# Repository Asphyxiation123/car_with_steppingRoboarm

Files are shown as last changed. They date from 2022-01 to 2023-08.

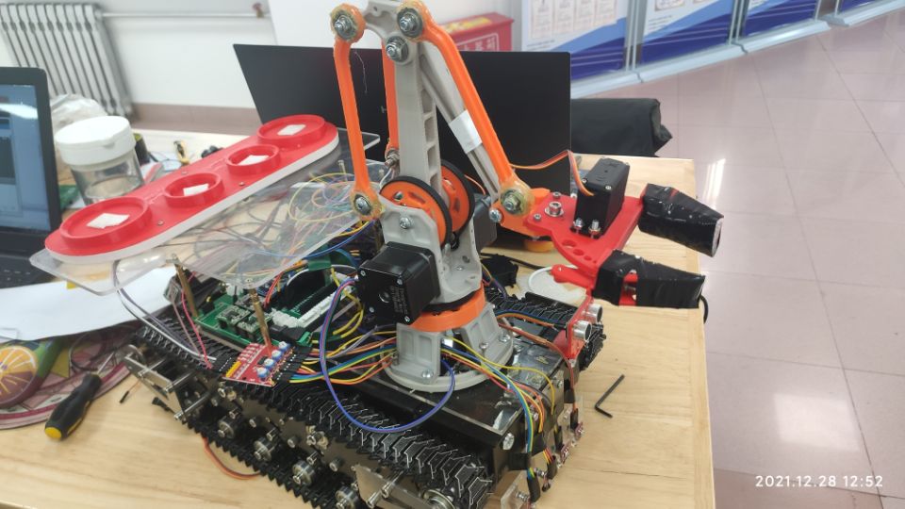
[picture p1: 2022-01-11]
【07】视频图片/图片/小车整体装配图.jpg

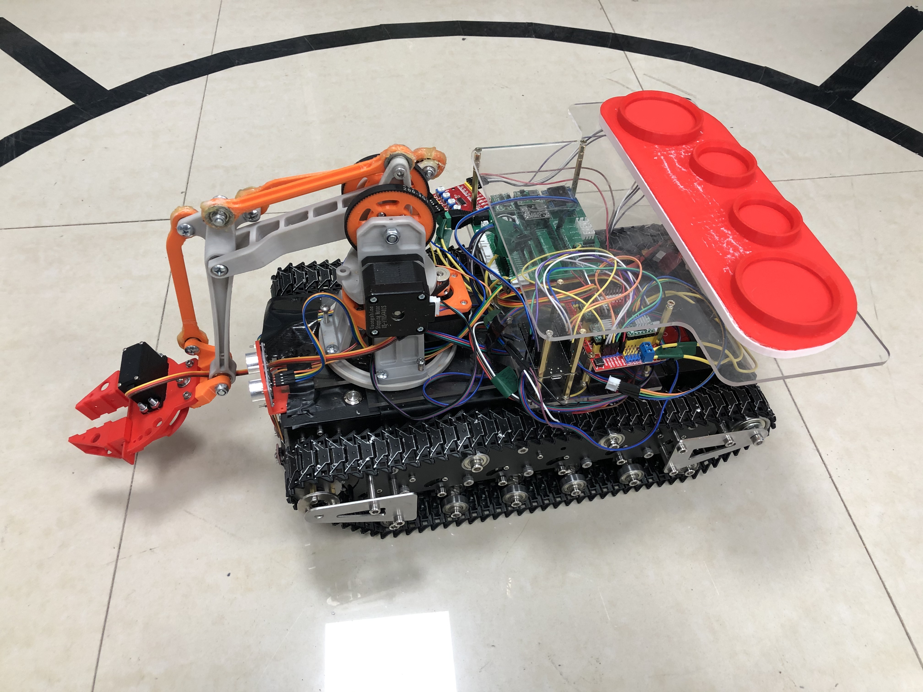
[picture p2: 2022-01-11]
【07】视频图片/图片/小车整体装配图2.jpg

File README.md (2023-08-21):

# car_with_stepperRoboarm
## 1. what's this
This is an course design in 2021,@YanShan University mechatronics engineering,
本仓库存放着自己带机械臂的循迹寻迹小车代码、模型，其借助点灯科技Blink还具有物联网功能。
## 2. 本代码结构
代码主要分为两部分，即Stm32主控制机械结构+esp32上传数据至电灯科技构成物联网系统,分别使用C与C++编写。小车控制用STM32实现，机械臂示教、控制与小车状态显示用ESP32控制。
### 2.1 物联网组态界面框架
其中物联网架构使用的是较为成熟的点灯科技自研的MQTT-UI界面通讯框架，使用方式与QT基本类似，相关资料见点灯科技官网官网。本此项目只要使用物联网组态界面进行小车所在节点实时同步与步进电机机械臂调试。
<video src="【07】视频图片/视频/蓝牙调试机械臂.mp4" controls></video>

### 2.2小车框架
小车运行逻辑为流程运行，但提前根据地图特征将地图分为数个节点，小车在不同节点上运行不同的流程逻辑，具体请见`[01]文档材料`部分。
# 文件架构分析
文件架构以在文件夹标题上有所体现，其中说明文档和介绍ppt可直接见`[01]文档材料`和`[02]PPT汇报`的最终版本，中间版本为进度汇报内容
机械部分图纸见`[03]二维图纸`，PCB电气部分图纸见`[06]嵌入式控制系统`的`电气原理图`部分。
.  
.  
  
.  
.1
.1
.
.
.1

.  
.  
.  
.  
.  

本课程设计的全部代码都由本人完成，真是见鬼，三个队友两个考研一个考公，我没猝死真是太好了。
2022.8.21：抱歉，其实我并不想抱怨上述内容，因为实际情况愿彼此

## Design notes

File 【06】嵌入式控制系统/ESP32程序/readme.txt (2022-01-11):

想要完整地打开项目文件请先按照其他中的教程或按照网络教程 https://www.bilibili.com/video/BV1tv411w74d?from=search&seid=10236622600450991913&spm_id_from=333.337.0.0
搭建好vscode+plateformio的环境，导入项目即可

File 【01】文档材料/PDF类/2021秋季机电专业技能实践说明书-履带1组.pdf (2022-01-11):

# 燕山大学

# 专 业 技 能 实 践 说 明 书

题 | 目： 智能化产线单元设计与制作——带取样
| AGV

### 学院（系）： 机械工程学院

### 年 级 专 业 ： 18 级机械电子工程

组 | 号： 5-履带 1 组
学 号 | 姓 名 | 成 绩
201811010426 | 陈嘉琛（70%）
201811010240 | 王玥灏（10%）
201811010022 | 刘欣源（10%）
201811010241 | 徐世杰（10%）
指 导 教 师 ： | 张连东 李玉昆
日 | 期： | 2021.12

## 燕山大学专业技能实践任务书

院（系）：机械工程学院 | 基层教学单位：机械电子工程系
组号 | 5 | 学生姓名 | 陈嘉琛
题目 | 智能化产线系统集成—履带取样 AGV
实 践 目 标 | 法律及环境等因素进行产品再开发，通过编写完整的程序，进行机器人运动控制规划，对作业过 程进行模拟仿真，最终高效地完成既定的协同作业任务。
实 践 要 求 | （1）运用现代信息技术获取产品相关信息； （2）动作特点能够充分展示机器人或 AGV 系统的结构特点，体现系统化设计思想； （3）整体方案要体现工作效率和经济性； （4）充分体现协同作业和团队合作； （5）动作时间 3-5 分钟。
工 作 量 | （1）资料查阅、方案准备、素材整理； （2）详细分析机器人系统的硬件和软件功能，制定运动控制方案； （3）完成机器人动作的总体规划； （4）编制程序设计流程图； （5）编写程序代码，控制机器人实现规划的动作； （6）程序调试、预演； （7）撰写专业综合训练说明书； （8）完成机器人规划动作的现场展示。
工 作 计 划 | （1）资料查阅、分析总结，所需天数 1 天 （2）运动控制方案设计，所需天数 2 天 （3）机器人动作的总体规划，所需天数 2 天 （4）程序流程图的设计，所需天数 1 天 （5）控制程序编码，所需天数 4 天 （6）程序调试，所需天数 2 天 （7）撰写综合训练说明书，所需天数 2 天 （8）答辩考核、演示，所需天数 1 天
参考 资料 | 通过校园网在我校订阅的电子资料库中可以搜索到大量的有关运动控制、单片机编程的参考 资料。同学们也可到学校的图书馆查找纸质期刊资料。机械学院的计算机中心上班时间免费对本 院学生开放，查阅外网资料。
指导教师签字 | | 基层教学单位主任签字

基于《机电产品设计》二级项目制作的智能机器人机械本体、传感检测、驱动及控制系统， 充分查阅文献，基于工程需求、作业任务、运动轨迹、信息交互等任务，同时考虑社会、安全、

说明：此表一式四份，学生、指导教师、基层教学单位、系部各一份。

年 月 日

## 燕山大学专业综合训练评审意见表

指导教师评语：

成绩：

指导教师：

年 | 月 | 日

答辩小组评语：

成绩：

评阅人：

年 | 月 | 日

课程设计总成绩：

答辩小组成员签字：

年 | 月 | 日

燕山大学专业综合训练说明书

4

目录

5

摘要

AGV 即自动导引小车,它多位一体,集结了当今科技领域先进的理论和应用技术,综 合了声、光、电、计算机等技术。AGV 具有灵活可靠、柔性化好、效率高、操作简便、 可控性强等许多优点,因此在柔性制造系统和自动化工厂中得到了广泛的应用,极大地提 高了企业的生产制造效率和自动化程度。将来的 AGV 必然向着更为简捷高效的方向发 展,会得到进一步推广,其应用领域也必然会随之变的更加广泛。 本项目综合研究分析了国内外 AGV 的发展情况和现状,并根据所学知识自主设计一 辆履带式 AGV 小车。主要设计工作有:机械总体方案设计（履带式底盘和机械臂的设计 或选型）、驱动电机的选取（底盘运行电机及机械臂运动所需电机）、各模块功能设计 选取（传感器、32 系统板、减压模块等）、各模块的实际连接设计、各零部件的强度校 核、基本控制系统分析、软件系统整体方案设计、硬件电路分析与绘制、小车运动学和 动力学分析、控制系统设计以及路径行驶规划策略。最终设计的物流小车能够实现自主 导引运行、运动轨迹的控制、自动循迹及避障、物联网监控组态、按照要求抓取和运输 工件等功能,目标是使其能够模拟现有的工厂实际使用的 AGV 物料运输小车，并绘制各 零件及外部电路原理图、机械装配图及相应的报告，熟悉前沿自动化控制与物联网监控 技术，完成此次项目。
关键词: 履带 AGV 小车 运动分析 自动控制 机械设计 物联网

6

## 第 1 章 产线工作方案介绍

### 1.1 产线简介 1.1.1 硬件系统框图

在整个产线的工作任务中，以 STM32F103C8T6 最小系统板为主控板，接收超声波 模块、四路红外循迹模块、扫码模块的信息，去控制履带底盘、机械臂、末端执行机构 的运行。

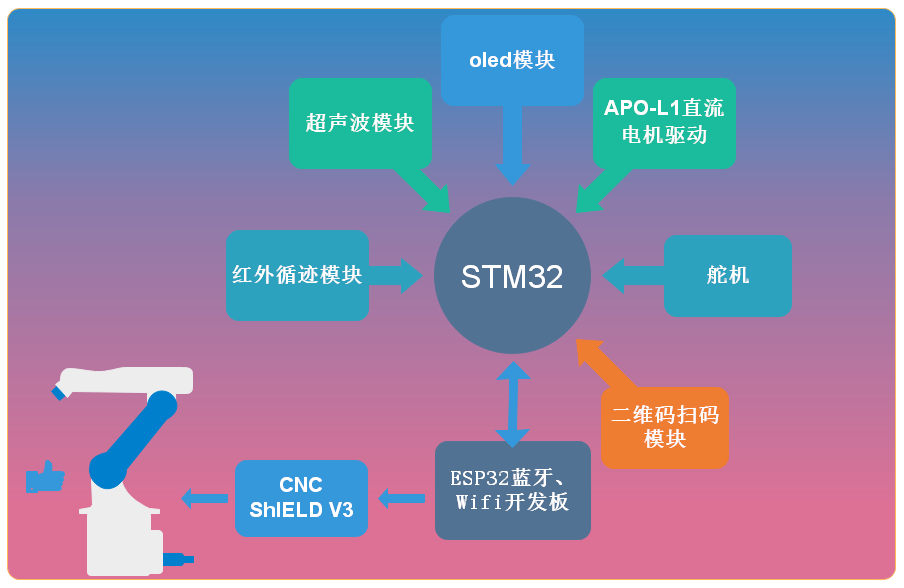
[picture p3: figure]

图 1.1 硬件系统框图

### 1.1.2 各单元硬件功能

表 1 各单元硬件功能

硬件 | 型号 | 功能
单片机 | STM32F103C8T6 | 主控单元，协调各模块的工作
固定降压模块 | MP1584EN（固定 3.3V） | 将电池提供的 12V 降为 3.3V，为板载模块供电
可调降压模块 | MP1584EN（0.8~22V 可调） | 为舵机组接口单独供电，保证舵机的稳定运行
直流电机驱动模块 | APO-L1 | 驱动底盘的两个直流电机
步进电机驱动模块 | A4988 | 驱动机械臂的三个步进电机
末端手爪驱动模块 | MG90S | 驱动末端手爪的张合
红外循迹模块 | 四路红外循迹模块 | 使小车检测并沿地面黑色迹线行驶
超声波模块 | HC-SR04 | 检测前方物体距离，以便停车避障
扫码模块 | SH-50 | 识别二维码，获取所需夹取的物料信息
显示模块 | 0.96inc OLED（IIC 显示屏） | 将关键信息显示，以便查看
Wifi 蓝牙模块 | ESP32 | 远程操控机械臂

7

### 1.2 产线单元的设计与实现

由于前期已经进行过各模块的选型，因此现阶段主要是根据场地任务要求，确定小 车的运行情况。

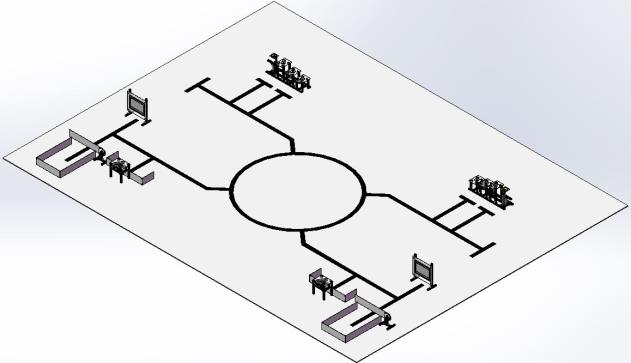
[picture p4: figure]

图 1.2 简化的场地模型

### 1.2.1 陈嘉琛同学方案设计及分析

AGV 履带小车产线单元，以 STM32F103C8T6 最小系统板为主控板，搭配超声波模 块、四路红外循迹模块、扫码模块，等外部传感设备，直流电机及其驱动器控制履带底 盘，步进电机及其驱动器控制机械臂和末端执行机构的运行。 开启开关后，超声波模块检测到开门后，STM32F103C8T6 最小系统板控制小车沿 着红外循迹模块识别到的路线到达扫码区扫描二维码，二维码中包含小车需要夹取货物 的信息。
然后继续寻迹至仓库区，使用自己设计的机械手按照二维码信息抓取预先放置好的 物块，接着小车携带货物沿预定路线返回。寻迹至组装区，小车在平台中心放料，完成 后返回仓库区重复取放货 2 次。

### 1.2.2 王玥灏同学方案设计及分析

AGV 履带小车产线单元，以 STM32F103C8T6 最小系统板为主控板，搭配超 声波模块进行避障功能、摄像头模块进行循迹和扫码功能，直流电机及其驱 动器控制履带底盘，步进电机及其驱动器控制机械臂和末端执行机构的运行。 开启开关后，超声波模块检测到开门后，STM32F103C8T6 最小系统板控制小车 沿着摄像头模块识别到的路线到达扫码区用摄像头扫描二维码，二维码中包 含小车需要夹取货物的信息。然后摄像头继续寻迹至仓库区，使用自己设计 的机械手按照摄像头扫描到的二维码信息抓取预先放置好的物块，接着小车 携带货物沿预定路线返回。寻迹至组装区，小车在平台中心放料，完成后返 回仓库区重复取放货 2 次。

### 1.2.3 刘欣源同学方案设计及分析

AGV 履带小车产线单元，以 STM32F103C8T6 最小系统板为主控板，搭配超声波模 块、四路红外循迹模块、扫码模块，等外部传感设备，直流电机及其驱动器控制履带底 盘，步进电机及其驱动器控制机械臂和末端执行机构的运行。 开启开关后，小车通过红外循迹模块识别并跟踪路线到达扫码区扫描二维码获取所 需夹取的物料，然后继续寻迹至仓库区，使用自己设计的机械手按照二维码信息抓取预

8

先放置好的物块，将所有需要夹取的物块放置小车上的货舱中，接着小车携带货物沿预 定路线返回。寻迹至组装区，小车将货舱中的物料放至平台中心，完成后返回至启动区。

### 1.2.4 徐世杰同学方案设计及分析

AGV 履带小车产线单元，以 STM32F103C8T6 最小系统板为主控板，搭配超声波模 块、四路红外循迹模块、扫码模块，等外部传感设备，直流电机及其驱动器控制履带底 盘，步进电机及其驱动器控制机械臂和末端吸盘的运行。
末端执行机构采用吸盘来进行对物块的抓取和释放，在接触物体时气泵吸气，吸盘 内部产生气压，将物块牢牢吸住，到达目标地点后放气，释放物块。采用气泵的优点有： 排放绿色无污染，物块抓取的程序设计更为简单，操作更方便。

### 1.2.5 小组方案讨论

陈嘉琛同学：王玥灏同学的方案中采用摄像头识别路线的方式虽然对于路线的跟踪更与 加明确和清晰，但较红外循迹而言过于复杂，不便于对设备的设计与调试。 王玥灏同学：刘欣源同学的方案一次抓取两个物块，对于大小物块的识别和抓取有一定 困难，且在小车上装货舱会给小车增加负重，若发生物块倾斜甚至倒下的情况，会严重 影响整体的完成速度。
刘欣源同学：徐世杰同学的方案中将夹爪换成了吸盘，吸盘需要增加检查整块的密封性， 在抓取物块时不能发生偏移，否则会发生不能将物块抓起的情况，若物块不规则，吸盘 将不能将物块抓起。
徐世杰同学：陈佳琛同学的方案需要往返抓取物块 2 次，严重增长了整体完成的时间， 远不如采用货舱的方式简便节省时间。

### 1.2.6 小组最终方案

我们最终决定采用以 STM32F103C8T6 最小系统板为主控板，搭配超声波模块、四 路红外循迹模块、扫码模块，等外部传感设备，直流电机及其驱动器控制履带底盘，步 进电机及其驱动器控制机械臂和末端执行机构的运行。采用末端机械爪并添加货舱只需 一次往返就完成的方案。

9

## 第 2 章 单元动作的总体规划详细方案

由图 1.2 所示，整个场地主要由数个转弯以及中间的圆形环岛迹线组成，由此规划 履带小车的整体动作。

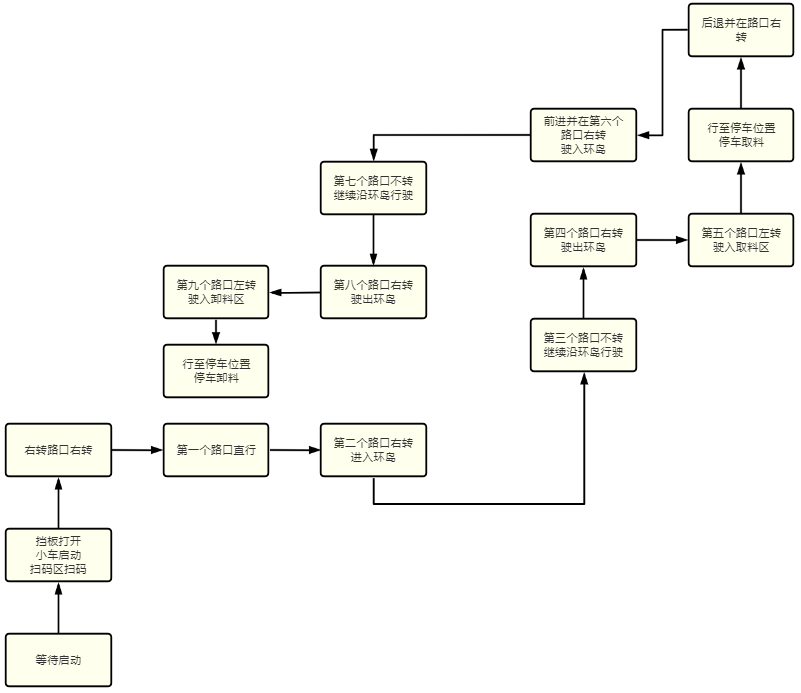
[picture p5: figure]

图 2.1 总体规划框图

## 第 3 章 编制程序设计流程及框图

根据场地组发布的任务要求，AGV 小车的工作流程为：
1、AGV 小车在启动区准备，舵机开门，开始计时，小车出发沿黑线寻迹，前往扫码区 扫描二维码，二维码中包含小车需要夹取货物的信息。
2、寻迹至仓库区，小车到达取货区，使用自带的机械手抓取预先放置好的物块，小车携 带货物返回。
3、寻迹至组装区，小车在平台中心放料，完成后返回仓库区重复取放货 2 次。 4、往返两次后，装箱结束，小车回到出发点，计时结束。
对小车的要求为：
1、小车尺寸，长：不超过 550mm 宽：不超过 360mm：高能正常抓取工件即可。小车 具有机械手用于工件抓取和搬运，手爪抓取最远距离参考需要结合取放货的空间位 置和自身车体大小设计，夹爪抓取物料最小重量为 150g。 2、小车应具有二维码扫描模块和黑线寻迹模块，自行选择红外避障模块和超声波测距模 块等其他传感器。
从 AGV 小车的工作流程及相关的硬件要求中，得出编程的流程：

10

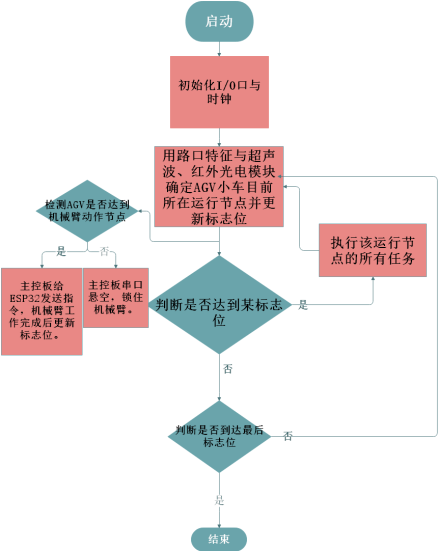
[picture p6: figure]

图 3.1 程序设计流程框图（陈嘉琛）

图 3.2 程序设计流程框图（王玥灏）

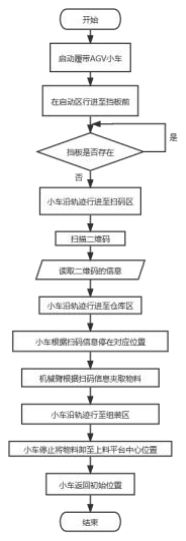
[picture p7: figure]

图 3.3 程序设计流程框图（刘欣源）

11

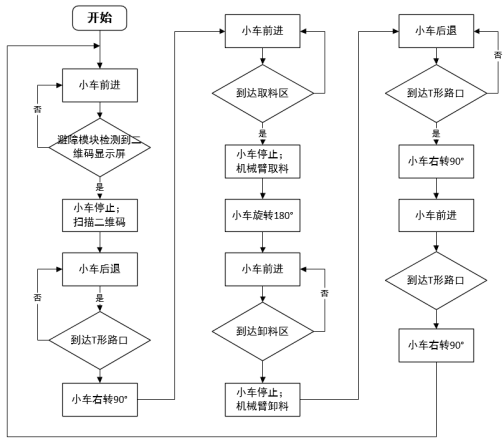
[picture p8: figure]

图 3.4 程序设计流程框图（徐世杰）

## 第4章 编程实现规划动作并编写程序代码

表 2 各硬件模块及负责人

负责人 | 硬件 | 型号
陈嘉琛 | 直流电机驱动模块 | TB6612FNG
| 步进电机驱动模块 | A4988
| Wifi 蓝牙模块 | ESP32
王玥灏 | 超声波模块 | HC-SR04
| 扫码模块 | SH-50
刘欣源 | 显示模块 | 0.96 寸 OLED（IIC 显示屏）
| 红外寻迹模块 | 四路红外循迹模块
徐世杰 | 红外循迹模块 | 四路红外循迹模块
| 末端手爪驱动模块 | MG995

### 4.1 直流电机驱动模块（APO-L1）

直流电机驱动模块用来驱动履带底盘的两个直流减速电机，该模块如图 4.1 所示。

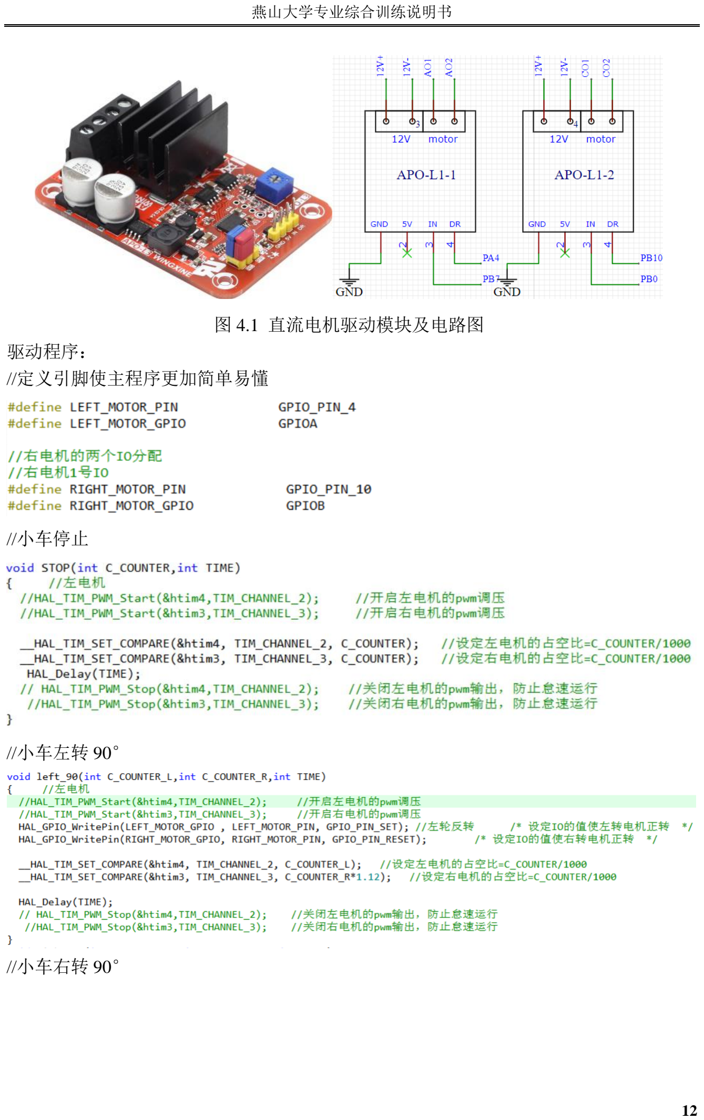
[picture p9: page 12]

12

图 4.1 直流电机驱动模块及电路图
驱动程序：
//定义引脚使主程序更加简单易懂

//小车停止

//小车左转 90°

//小车右转 90°

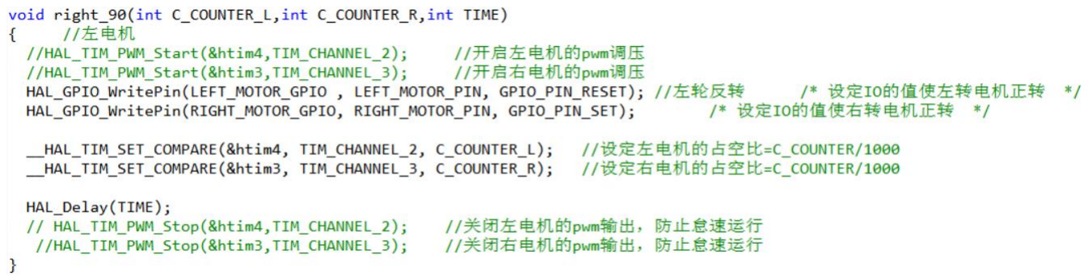
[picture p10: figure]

13

//小车掉头

### 4.2 步进电机驱动模块（A4988）

步进电机驱动模块用来驱动机械臂的三个步进电机，控制机械臂的动作，该模块如 图 4.5 所示。

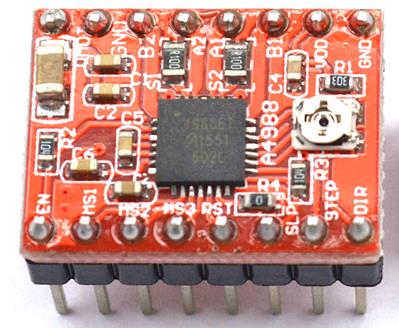
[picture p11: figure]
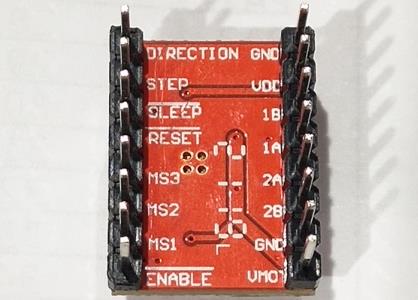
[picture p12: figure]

图 4.2 步进电机驱动模块（A4988）
对于 A4988 来说，ENA 为使能端，低电平有效；STEP 为步进电机信号的输入端， 可以采用 PWM 波输入，也可以采用 IO 引脚高低电平转换；MS1、MS2、MS3 控制一 个脉冲旋转多少度，分别是全步进，1/2 步进，1/4 步进，1/8 步进，1/16 步进模式，如 表所示；DIR 为步进电机方向控制 IO 高电平为顺时针，低电平为逆时针；VDD 为模块 的逻辑电压 3V3 或 5V，VDD 必须接电；VMOT 为步进电机的输入电压（8V-35V）；1A、 1B 为同一相，2A、2B 为同一相，不能接反，否则电机会出现抖动的情况。对于步进电 机同一相的确定方法是：将电压表打到蜂鸣器档位，将正负表笔随意接步进电机的两个 引脚，若蜂鸣器响起，则该两引脚为一相。
综上，控制 MS1、MS2、MS3、STEP、DIR 就可以控制一个步进电机的运行了，甚 至只用 STEP 就可以了。
引脚 | MS1 | MS2 | MS3 | 步进模式
引脚 电平 | L | L | L | 全步进
| H | L | L | 1/2 步进

14

L | H | L | 1/4 步进
H | H | L | 1/8 步进
H | H | H | 1/16 步进
//将接收二维码传递的数据进行转换，确定夹取物块的顺序

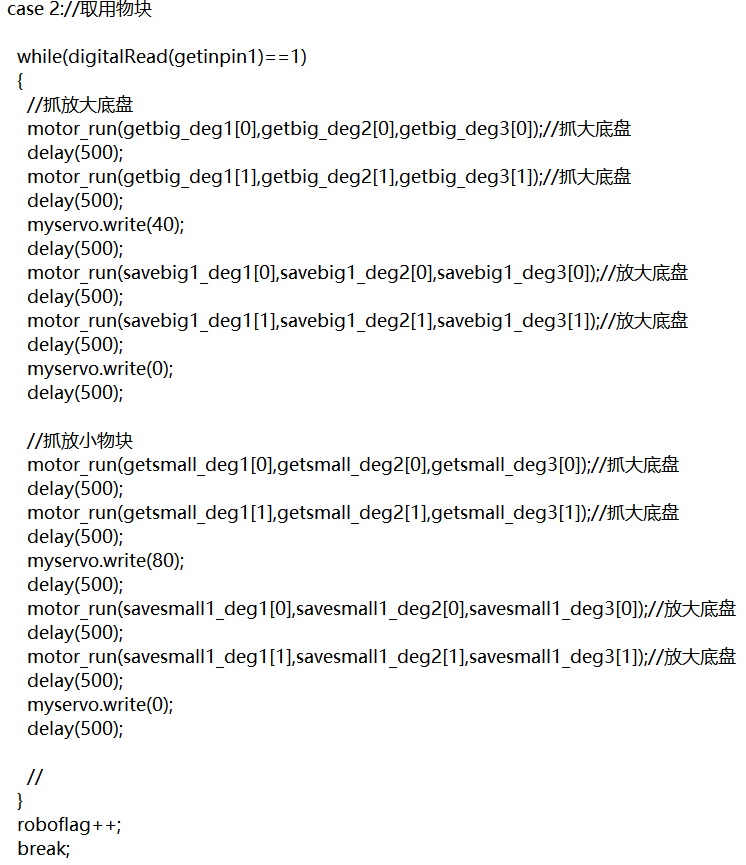
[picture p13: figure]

15

16

17

### 4.3 末端手爪驱动模块（MG995）

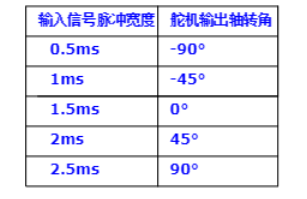
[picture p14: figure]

图 4.3 舵机转角数据图

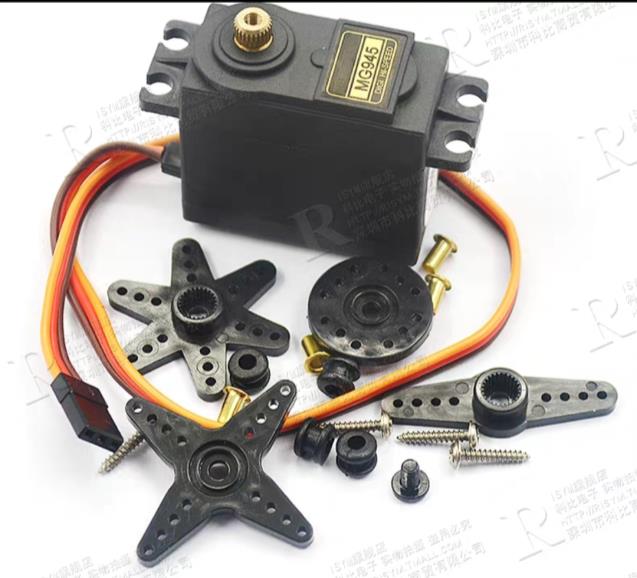
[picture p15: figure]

图 4.4 末端手抓驱动模块
程序已加入步进电机的夹取部分，详细如 4.2 步进电机驱动模块（A4988）所述程序

### 4.4 超声波模块（HC-SP04）

超声波模块装在履带底盘小车的前方，用来检测与前方物体的距离，以便小车及时 减速避让或停车。该模块如图 4.6 所示。

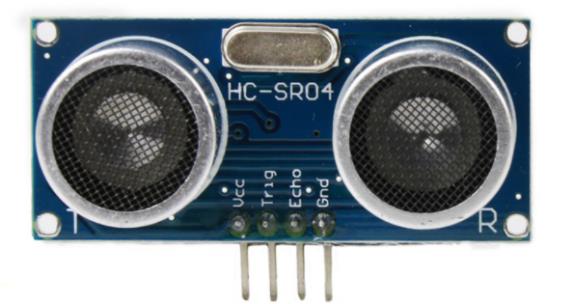
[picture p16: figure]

图 4.5 超声波模块（HC-SR04）
超声波模块程序的编写参考图 4.7 的时序图，时序图表明，只需要提供一个 10uS 以

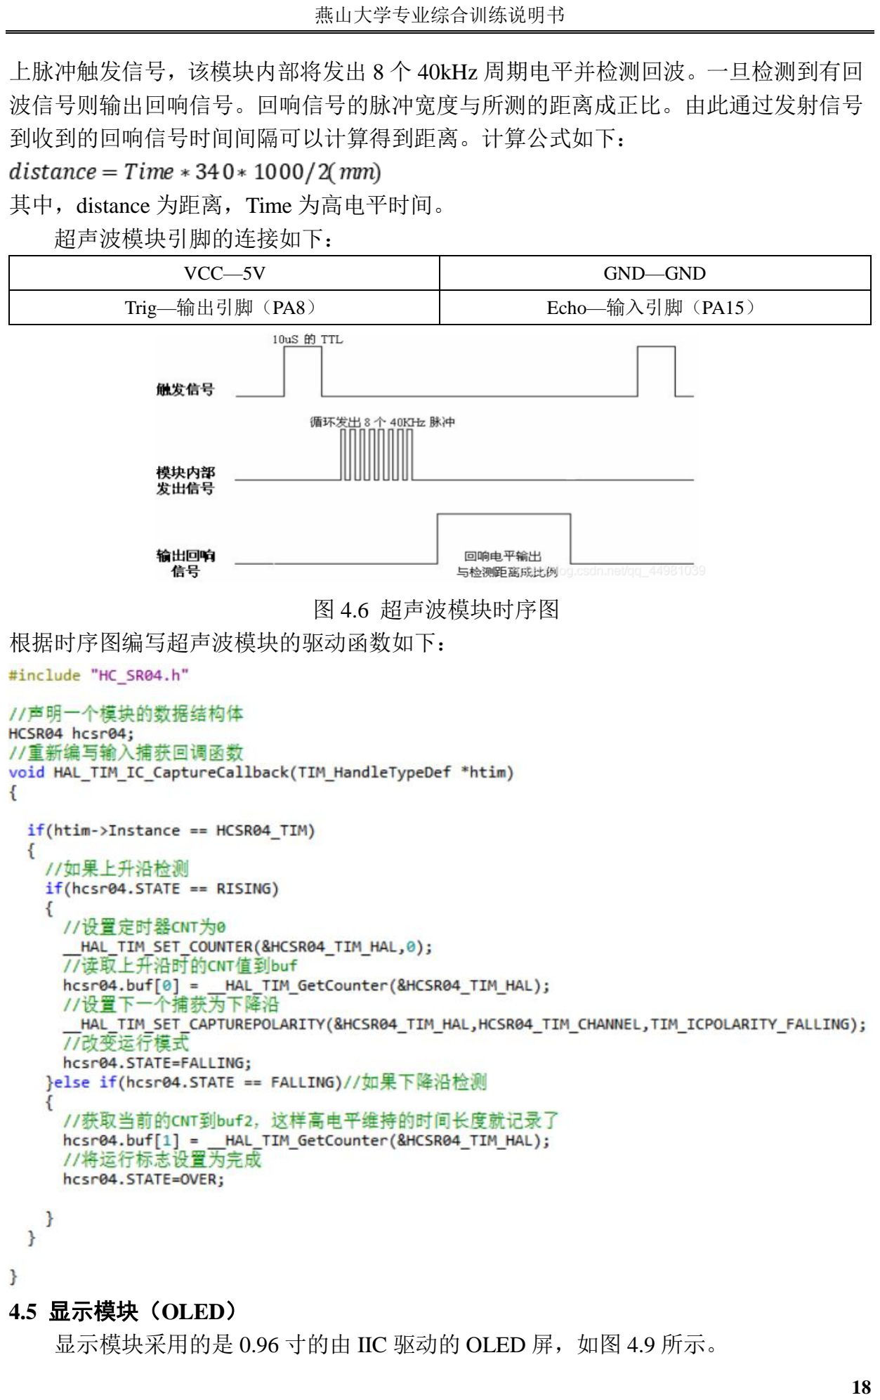
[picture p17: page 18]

18

上脉冲触发信号，该模块内部将发出 8 个 40kHz 周期电平并检测回波。一旦检测到有回 波信号则输出回响信号。回响信号的脉冲宽度与所测的距离成正比。由此通过发射信号 到收到的回响信号时间间隔可以计算得到距离。计算公式如下：

其中，distance 为距离，Time 为高电平时间。
超声波模块引脚的连接如下：
VCC—5V | GND—GND
Trig—输出引脚（PA8） | Echo—输入引脚（PA15）

图 4.6 超声波模块时序图
根据时序图编写超声波模块的驱动函数如下：

### 4.5 显示模块（OLED）

显示模块采用的是 0.96 寸的由 IIC 驱动的 OLED 屏，如图 4.9 所示。

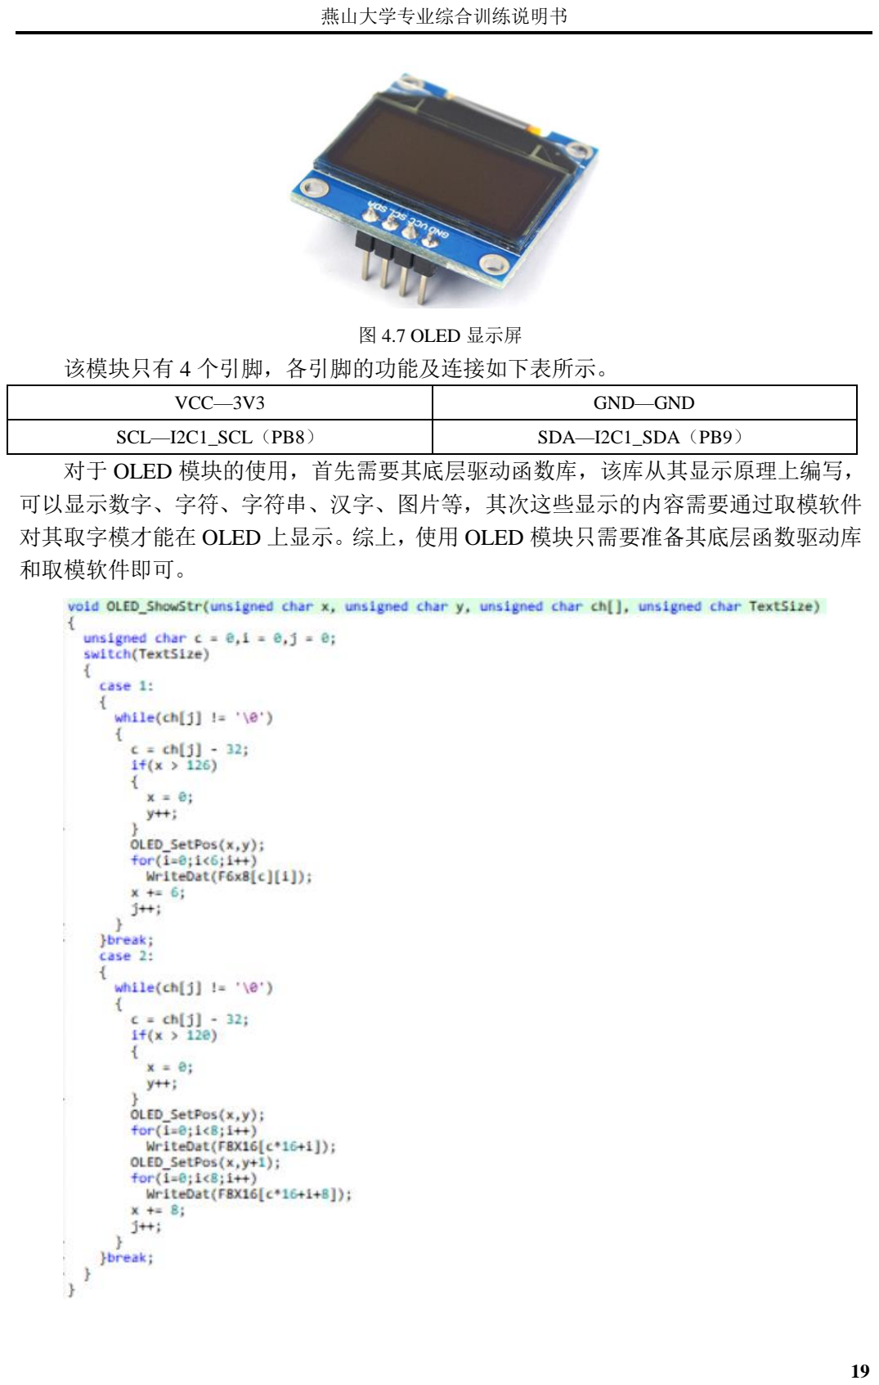
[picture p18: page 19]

19

图 4.7 OLED 显示屏
该模块只有 4 个引脚，各引脚的功能及连接如下表所示。
VCC—3V3 | GND—GND
SCL—I2C1_SCL（PB8） | SDA—I2C1_SDA（PB9）
对于 OLED 模块的使用，首先需要其底层驱动函数库，该库从其显示原理上编写， 可以显示数字、字符、字符串、汉字、图片等，其次这些显示的内容需要通过取模软件 对其取字模才能在 OLED 上显示。综上，使用 OLED 模块只需要准备其底层函数驱动库 和取模软件即可。

20

### 4.6 扫码模块（SH-50）

在场地组的要求中，小车首先要在启动区进行扫码，得到需要夹取的物料的信息， 然后小车才能出发。
扫码模块使用的是上海斯恳赫公司生产的 SH-50 型扫码模块，如图 4.11 所示。该模 块可以直接通过串口将扫码信息发送到上位机，中间无需人为转换。但在项目实施中， 小车要自我识别扫码信息，不能人为操控，因此该模块的使用主要是将扫码得到的信息 进行处理，使单片机能识别。

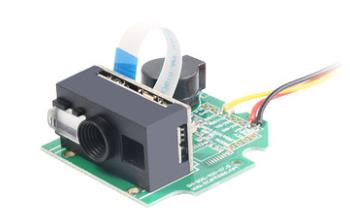
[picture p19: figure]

图 4.8 扫码模块（SH-50）
在该扫码模块上自带串口功能，因此单片机需要通过串口与该模块通讯。如图 4.12 所示，首先在单片机中预设好扫码要得到的信息，以“01234567”为例，将信息进行拆 分提取。

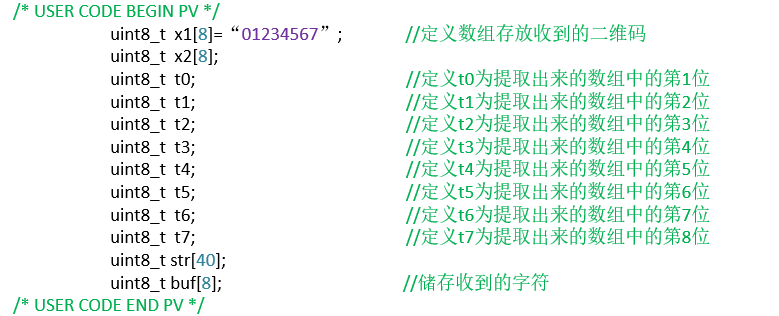
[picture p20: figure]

### 4.7 红外寻迹模块（四路红外循迹模块）

红外循迹模块负责检测地面的黑色迹线，控制履带底盘的前进、左转、右转等动作， 如图 4.14 所示。

21

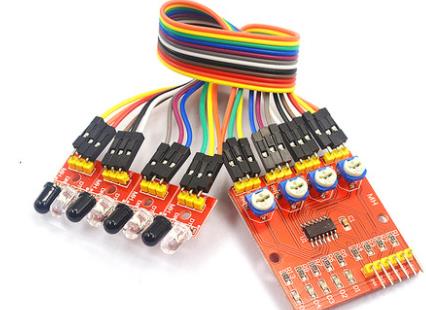
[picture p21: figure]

图 4.9 红外循迹模块（四路红外循迹）
对于该循迹模块，黑色 led 发出红外光，经反射后由白色 led 接收。当物体的颜色较 白时，反射的红外光较多，此时模块上对应的 D 口 led 亮，此时输出低电平；当物体的 颜色较深时，吸收的红外光较多，反射的较少，此时模块上对应的 D 口 led 灭，此时输 出高电平。模块上有对应的电位器，调节电位器即可调节相应循迹模块的灵敏度。因此， 对于该模块的编程，主要是读取相应引脚的高低电平去改变履带底盘电机的转速和转向 即可。
四路红外循迹模块控制履带底盘直流电机的部分程序如图 4.15 所示，当中间两路检 测到高电平时，说明此时为直线，车体居中，底盘直走；当中间两路任意一路为低电平 时，说明此时车体向该路偏转，需要将该路侧的电机转速加大，使其归正，以此类推。

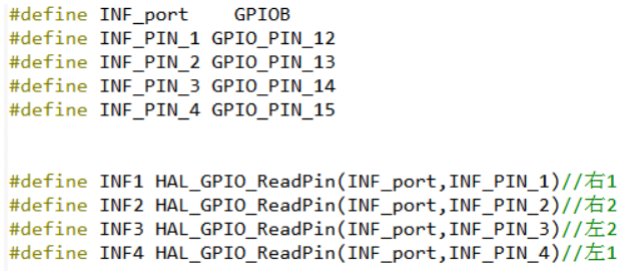
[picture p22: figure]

//小车循迹

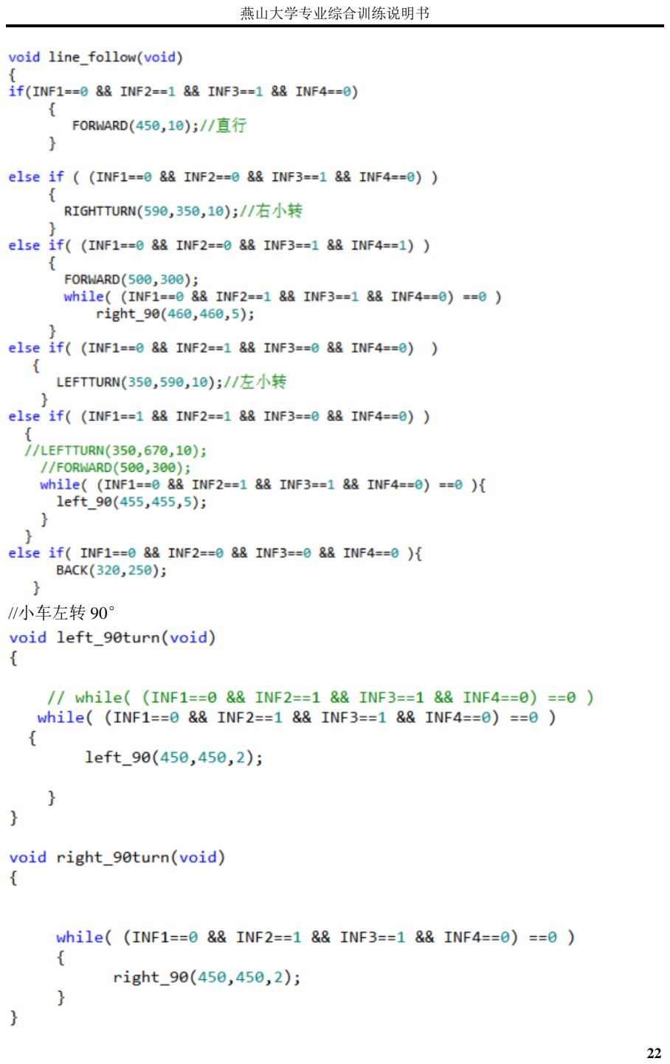
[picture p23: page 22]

22

//小车左转 90°

23

//小车环岛循迹

### 4.8 Wifi 蓝牙模块（ESP32）

Wifi 蓝牙模块 ESP32 用以辅助控制机械臂的运动。

图 4. 10 ESP32 引脚分配功能图

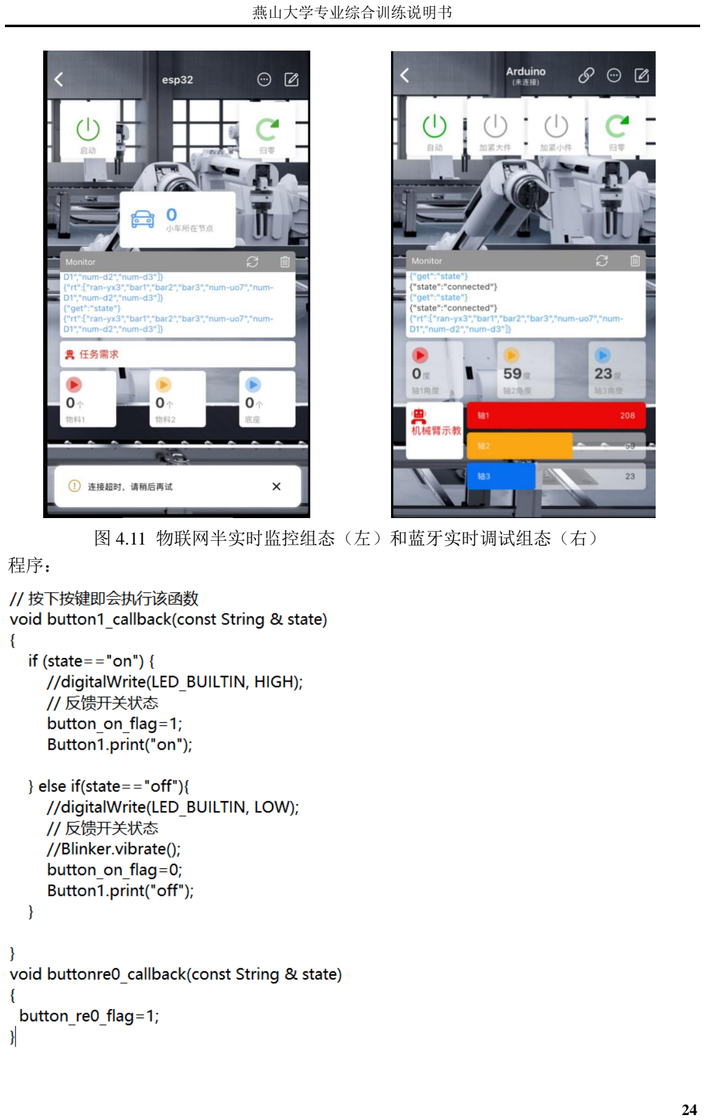
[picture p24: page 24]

24

图 4.11 物联网半实时监控组态（左）和蓝牙实时调试组态（右） 程序：

25

## 第 5 章 程序调试结果及改进

程序调试过程中，对于有些模块，只要给定固定的程序就能够正确运行。因此只对 其中直流电机模块、超声波模块、红外寻迹模块和显示的调试进行阐述。

### 5.1 直流电机模块的调试（陈嘉琛）

在直流电机模块的调试过程中，最开始采用的是 TB6612FNG，多次调试却总是只 有一个履带可以运行，所以想到是否是这种模块的电压太小，所以就更换成了 APO-L1， 发现的确是 TB6612FNG 带不动直流电机。把左右两个直流电机的占空比设置为相同值， 理论上两个直流电机的转速应该相同，但经过数十次的循迹过后，发现在相同占空比的 条件下，履带小车在走直线时，车体总会往左偏，即左轮速度会比右轮速度快。随后经 过数次尝试，找出了合适的占空比，如图 5.1 所示，使履带小车在进行直线循迹时，能 尽量保持在中位。

### 5.2 超声波模块的调试（王玥灏）

在超声波模块的调试中，很重要的一个因素是电源的供给必须是 5V，如果使用的是 3V3 的电源，即使程序编写正确，超声波测出的距离也会不准确或者没有变化，对于排 查程序的错误也会增加很多困难。
最开始是在 NUCLEO 开发板上进行程序的编写实验的，成功驱动之后需要移植到 STM32F103C8T6 最小系统板上，但在移植之后，发现超声波模块不能正常使用，连值 都不能输出。在经过两部分程序及 CubeMX 设置的对比之后发现，NUCLEO 开发板上 自带旁路时钟源，而 STM32F103C8T6 最小系统板上没有，因此照搬 NUCLEO 的设置的 行不通，最后把 HSE 选项选到 Disable 之后，如图 5.3 所示，超声波模块就能正常运行 了。

### 5.3 红外寻迹模块的调试（刘欣源）

红外循迹模块的调试主要是灵敏度和模块之间的间距。红外循迹模块的灵敏度是单 片机能正常触发相关程序的关键，其灵敏度是通过模块上相关 led 小灯的亮灭来体现的， 有一个最大的误区就是当小灯微微亮时，输出的是高电平，很容易导致信号错误，使小 车发生错误判断。所以在调试时，相关 led 小灯只能出现非亮即灭两种情况，否则容易 导致单片机错误判断。另外是在直射光较强时，地面的黑色迹线反射的光线也较强，会 使红外循迹模块接收到相关的红外信号，即把此处判断为低电平，会使小车莫名停车， 但遮挡相关干扰光线之后，就能使小车正常工作。环境过暗也同理，会使红外循迹模块 把本该识别为低电平的地方识别成高电平，使小车误判，因此环境的光线也极为重要。 红外循迹模块的间距的主要是配合场地的 50mm 黑色迹线，在直线情况时，本组使 用中间两个模块位于黑色迹线中间，两边的红外模块在黑色迹线之外，四个红外循迹模 块在水平和竖直方向的同一平面上。若红外循迹模块之间的间距过宽，会使履带小车在 过圆形环岛迹线时，不容易判断路口，进行计数识别；若红外循迹模块之间的间距过窄， 会使履带小车频繁的调整车体姿态，影响履带小车的行走，并且会增大红外循迹模块之 间的干扰，造成误检测。

### 5.4 显示模块的调试（徐世杰）

显示模块即 OLED 模块程序的调试主要是换行显示及动态刷新的程序调试。

26

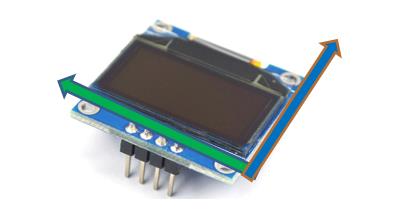
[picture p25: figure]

图 5.1 OLED 模块
换行显示的目的是使 OLED 屏能显示更多相关信息。如图 5.4 所示，在绿色箭头方 向，OLED 有 128 个像素点；在蓝色箭头方向，OLED 分为 8 页，每页共 8 个像素点。 在取模软件输出的字的大小一般为 16×16 个像素的大小，因此可以知道，每个字或数字 等，在绿色箭头方向占 16 个像素点，在蓝色箭头方向占 2 页，所以可以写出换行程序如 图 5.5 所示。

图 5.5 OLED 换行程序（部分）
其次是 OLED 显示动态刷新内容，此功能可以配合超声波模块的测距和检测四路红 外循迹模块的使用。调试的思路是：首先定义一个数组，将外部输入进来的信号存到此 数组之中，再采用 sprintf 函数将其打印，最后通过 OLED 显示函数将其发送到显示页面 上。

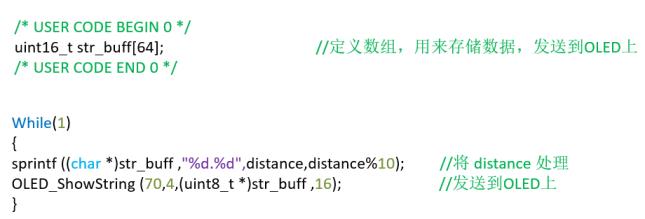
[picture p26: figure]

图 5.2 OLED 动态刷新显示内容

27

## 第 6 章 项目思政心得体会

陈嘉琛：
经过本次二级项目，我们将二级项目中遇到的问题和困难进行了思考总结，对所使用的 stm32cube，keil 等软件和机械臂机器人，还有红外循迹模块，超声波模块等传感器有 了进一步的认识；通过本次二级项目，我们除了提高了软件的操作能力，也明白了团队 合作的重要性，没有大家的共同努力，是无法将本次项目做好的。相信我们日后对待更 加复杂的问题时，也能处理地更加完善。
王玥灏：
通过此次二级项目的实施，我们对机器人技术，机械动力学分析，嵌入式，传感器，机 电一体化等课程有了更深的认识。“纸上得来终觉浅，绝知此事要躬行”。在没有开始 实验之前，对于二级项目有点自己上了就能行的感觉。等到真正的上手操作时，却发现 自己终究是眼高手低，各种各样的问题层出不穷，最终在通力合作下才完成了项目。学 习的路上任重道远，我们要保持终身学习的好习惯，才能站在时代的风口而屹立不倒。 刘欣源：
通过查阅相关文献资料与小组内部讨论，在小组的共同努力下，完成了本次二级项目。 本次项目涉及了嵌入式，机器人技术等课程，对这些学过的课程有了更深刻的认识。二 级项目训练了我们如何查资料及绘图、数据处理、创新能力，培养了我们独立设计机电 一体化产品的能力，提高我们综合应用已有知识解决问题的能和综合素质。同时加强团 队协作能力，促进交流与合作，拓展视野，勇于创新，提高思考与决策水平，形成解决 实际问题的能力和终身学习的能力。
徐世杰：
在本次二级项目中，合理分工，通力合作，每位成员都发挥了自己相对应的价值，对本 次课程设计做出了很大的贡献，我们了收获很多，在设计过程中大家一起讨论，分工合 作，相互帮助，使得项目顺利完成。在这个项目过程中同样也会有很多的意见，通过团 结合作，我们最终完善了这个项目。同时，这次项目使我们把过去一个段时间所学的理 论知识融会贯通，真正了解理论知识在工程实际中的应用，提高了解决实际问题的能力， 锻炼了主动学习及查阅资料的能力。

28

## 参考文献

[1] 闻邦椿 机械设计手册.[M](第一版)，北京，机械工业出版社，2010 年 1 月，
[2] 钱晓捷 [程 楠] 嵌入式系统导论[M]（第四版），北京，电子工业出版社，2020 年 2 月
[3] 许立忠 [周玉林] 机械设计[M] （第三版），北京，中国标准出版社，2019 年 9 月
[4] 龚溎义 [严国良] 设计课程设计图册（第三版），北京，高等教育出版社，2019 年 12 月

29

## 附录 1 程序源代码

//linetracking.h 宏定义部分程序，可以使主程序更简洁 #define INF1 HAL_GPIO_ReadPin(INF_port,INF_PIN_1)//右 1 #define INF2 HAL_GPIO_ReadPin(INF_port,INF_PIN_2)//右 2 #define INF3 HAL_GPIO_ReadPin(INF_port,INF_PIN_3)//左 2 #define INF4 HAL_GPIO_ReadPin(INF_port,INF_PIN_4)//左 1

//linetracking.c 程序

#include "linetracking.h"

#include "motor.h"

#include "stm32f1xx_hal.h"

extern uint8_t flag_reach;
void linetrack(void)
{
if(INF1==0 && INF2==1 && INF3==1 && INF4==0) {
FORWARD(450,10);//直行

}
else if ( (INF1==0 && INF2==0 && INF3==1 && INF4==0) )
{
RIGHTTURN(500,350,10);//右小转

}
else if ( (INF1==0 && INF2==0 && INF3==0 && INF4==1) ||(INF1==0 && INF2==0 && INF3==1 && INF4==1)) {
RIGHTTURN(650,370,10);//右 da 转

}
else if( (INF1==0 && INF2==1 && INF3==0 && INF4==0) ) {
LEFTTURN(350,500,10);//左小转

}
else if( (INF1==1 && INF2==0 && INF3==0 && INF4==0) ||(INF1==1 && INF2==1 && INF3==0 && INF4==0) ) {
LEFTTURN(350,680,10);//左 da 转

}

30

else if(INF1==0 && INF2==0 && INF3==0 && INF4==0) {
STOP(0,100);
BACK(350,400);
}
else if(INF1==1 && INF2==1 && INF3==1 && INF4==1) {
STOP(0,50);//停转

if(INF1==1 && INF2==1 && INF3==1 && INF4==1){ STOP(0,50);//停转

flag_reach=1;
HAL_GPIO_WritePin(led_GPIO_Port,led_Pin,GPIO_PIN_SET); rotate_180(420,420,3000);
while( (INF1==0 && INF2==1 && INF3==1 && INF4==0) ==0 ) rotate_180(420,420,10);
}
}
else if(INF1==1 && INF2==1 && INF3==1 && INF4==0) {
STOP(0,50);//停转

if(INF1==1 && INF2==1 && INF3==1 && INF4==0)
{
while( (INF1==0 && INF2==1 && INF3==1 && INF4==0) ==0 ) left_90(330,580,10);
}
}
void line_follow(void)
{
if(INF1==0 && INF2==1 && INF3==1 && INF4==0) {
FORWARD(450,10);//直行

}

else if ( (INF1==0 && INF2==0 && INF3==1 && INF4==0) ) {
RIGHTTURN(590,350,10);//右小转

}
else if( (INF1==0 && INF2==0 && INF3==1 && INF4==1) ) {

31

FORWARD(500,300);
while( (INF1==0 && INF2==1 && INF3==1 && INF4==0) ==0 ) right_90(460,460,5);
}
else if( (INF1==0 && INF2==1 && INF3==0 && INF4==0) ) {
LEFTTURN(350,590,10);//左小转

}
else if( (INF1==1 && INF2==1 && INF3==0 && INF4==0) ) {
//LEFTTURN(350,670,10);
//FORWARD(500,300);
while( (INF1==0 && INF2==1 && INF3==1 && INF4==0) ==0 ){ left_90(455,455,5);
}
}
else if( INF1==0 && INF2==0 && INF3==0 && INF4==0 ){ BACK(320,250);
}
}
void left_90turn(void)
{
// while( (INF1==0 && INF2==1 && INF3==1 && INF4==0) ==0 ) while( (INF1==0 && INF2==1 && INF3==1 && INF4==0) ==0 )
{
left_90(450,450,2);
}
}
void right_90turn(void)
{
while( (INF1==0 && INF2==1 && INF3==1 && INF4==0) ==0 ) {
right_90(450,450,2);
}
}
void circle_turn(void)
{
if(INF1==0 && INF2==1 && INF3==1 && INF4==0) {

32

FORWARD(420,2);//直行

}
else if ( (INF1==0 && INF2==0 && INF3==1 && INF4==0) ||(INF1==0 && INF2==0 && INF3==1 && INF4==1) ) {
RIGHTTURN(675,350,5);//右小转

}
else if( (INF1==0 && INF2==1 && INF3==0 && INF4==0) ||(INF1==1 && INF2==1 && INF3==0 && INF4==0) ) {
LEFTTURN(350,670,5);//左小转

}
else if( INF1==0 && INF2==0 && INF3==0 && INF4==0 ){ BACK(330,40);
}
}
uint8_t T_check(void)
{
if(INF1==1 && INF2==1 && INF3==1 && INF4==1)
{
STOP(0,50);//停转

if(INF1==1 && INF2==1 && INF3==1 && INF4==1) {
return 1;
}
else
return 0;
}
else
return 0;
}
uint8_t left90_check(void)
{
if(INF1==1 && INF2==1 && INF3==1 && INF4==0)
{
STOP(0,50);//停转

if(INF1==1 && INF2==1 && INF3==1 && INF4==0) {
return 1;

33

}
else
return 0;
}
else
return 0;
}
uint8_t right90_check(void)
{
if(INF1==0 && INF2==1 && INF3==1 && INF4==1)
{
STOP(0,50);//停转

if(INF1==0 && INF2==1 && INF3==1 && INF4==1) {
return 1;
}
else
return 0;
}
else
return 0;
}
uint8_t right_180turn(void)
{
right_90(440,440,800);
while( (INF1==0 && INF2==1 && INF3==1 && INF4==0)==0 ) {
right_90(440,440,2);
}
return 1;
}
void line_follow_slowdown(void)
{
if(INF1==0 && INF2==1 && INF3==1 && INF4==0) {
FORWARD(380,5);//直行

}
else if ( (INF1==0 && INF2==0 && INF3==1 && INF4==0) ) {

34

RIGHTTURN(490,340,10);//右小转

}
else if( (INF1==0 && INF2==0 && INF3==1 && INF4==1) ) {
FORWARD(500,300);
while( (INF1==0 && INF2==1 && INF3==1 && INF4==0) ==0 ) right_90(460,460,5);
}
else if( (INF1==0 && INF2==1 && INF3==0 && INF4==0) ) {
LEFTTURN(340,490,10);//左小转

}
else if( (INF1==1 && INF2==1 && INF3==0 && INF4==0) ) {
//LEFTTURN(350,670,10);
//FORWARD(500,300);
while( (INF1==0 && INF2==1 && INF3==1 && INF4==0) ==0 ){ left_90(455,455,5);
}
}
else if( INF1==0 && INF2==0 && INF3==0 && INF4==0 ){ BACK(320,250);
}
}
uint8_t middle_check(void)
{
if(INF1==0 && INF2==1 && INF3==1 && INF4==0) {

HAL_Delay(20);//
if(INF1==0 && INF2==1 && INF3==1 && INF4==0) {
return 1;
}
else
return 0;
}
else
return 0;

35

}
void dongyidong(void)
{
FORWARD(400,2000);
BACK(400,2000);
left_90(450,450,1000);
right_90(450,450,1000);
}

//motor.c 直流电机运行程序

#include "motor.h"

#include "tim.h"

//左转函数
/* 注：电机输入 IO 口 1 表示正转，0 表示反转
PWM 口输入 0--1000 值进行速度调节

*/
void LEFTTURN(int C_COUNTER_L,int C_COUNTER_R,int TIME_L) { //左电机

//HAL_TIM_PWM_Start(&htim4,TIM_CHANNEL_2);
//开启左电机的 pwm 调压
__HAL_TIM_SET_COMPARE(&htim4, | TIM_CHANNEL_2, | C_COUNTER_L);
//设定左电机的占空比=C_COUNTER/1000
HAL_GPIO_WritePin(LEFT_MOTOR_GPIO | , | LEFT_MOTOR_PIN,
GPIO_PIN_RESET); //左轮正转 | /* 设定 IO 的值使左转电机正转或反转 */
//右电机

// HAL_TIM_PWM_Start(&htim3,TIM_CHANNEL_3);
//开启右电机的 pwm 调压

__HAL_TIM_SET_COMPARE(&htim3, TIM_CHANNEL_3, C_COUNTER_R*1.2); //设定右电机的占空比=C_COUNTER/1000

HAL_GPIO_WritePin(RIGHT_MOTOR_GPIO, | RIGHT_MOTOR_PIN,
GPIO_PIN_RESET); | /* 设定 IO 的值使右转电机正转或反转 */
//设定运行时间

HAL_Delay(TIME_L);
// | HAL_TIM_PWM_Stop(&htim4,TIM_CHANNEL_2); | //关闭左电机的 pwm 输
出，防止怠速运行
// | HAL_TIM_PWM_Stop(&htim3,TIM_CHANNEL_3); | //关闭右电机的 pwm 输
出，防止怠速运行

}

36

//右转函数

void RIGHTTURN(int C_COUNTER_L,int C_COUNTER_R,int TIME_R)
{ | //左电机
// | HAL_TIM_PWM_Start(&htim4,TIM_CHANNEL_2);
//开启左电机的 pwm 调压

__HAL_TIM_SET_COMPARE(&htim4, TIM_CHANNEL_2, C_COUNTER_L); //设定左电机的占空比=C_COUNTER/1000

HAL_GPIO_WritePin(LEFT_MOTOR_GPIO | , | LEFT_MOTOR_PIN,
GPIO_PIN_RESET); | /* 设定 IO 的值使左转电机正转或反转 */

//右电机

// | HAL_TIM_PWM_Start(&htim3,TIM_CHANNEL_3);
//开启右电机的 pwm 调压
__HAL_TIM_SET_COMPARE(&htim3, | TIM_CHANNEL_3,
C_COUNTER_R*1.12); | // 设定右电机的占空比

=C_COUNTER/1000
HAL_GPIO_WritePin(RIGHT_MOTOR_GPIO, | RIGHT_MOTOR_PIN,
GPIO_PIN_RESET); | /* 设定 IO 的值使右转电机正转或反转 */
//设定运行时间

HAL_Delay(TIME_R);
// | HAL_TIM_PWM_Stop(&htim4,TIM_CHANNEL_2); | //关闭左电机的 pwm 输
出，防止怠速运行
// | HAL_TIM_PWM_Stop(&htim3,TIM_CHANNEL_3); | //关闭右电机的 pwm 输
出，防止怠速运行

}

//前进函数

void FORWARD(int C_COUNTER,int TIME)
{ //左电机

//HAL_TIM_PWM_Start(&htim4,TIM_CHANNEL_2);
//开启左电机的 pwm 调压

__HAL_TIM_SET_COMPARE(&htim4, TIM_CHANNEL_2, C_COUNTER); //设定左电机的占空比=C_COUNTER/1000

HAL_GPIO_WritePin(LEFT_MOTOR_GPIO | , | LEFT_MOTOR_PIN,
GPIO_PIN_RESET); | /* 设定 IO 的值使左转电机正转或反转 */
//右电机
// | HAL_TIM_PWM_Start(&htim3,TIM_CHANNEL_3);
//开启右电机的 pwm 调压
__HAL_TIM_SET_COMPARE(&htim3, | TIM_CHANNEL_3,

37

C_COUNTER*1.12); | //设定右电机的占空比=C_COUNTER/1000
HAL_GPIO_WritePin(RIGHT_MOTOR_GPIO, | | RIGHT_MOTOR_PIN,
GPIO_PIN_RESET); | /* 设定 IO 的值使右转电机正转或反转 */
//设定运行时间

HAL_Delay(TIME);
// HAL_TIM_PWM_Stop(&htim4,TIM_CHANNEL_2);
// HAL_TIM_PWM_Stop(&htim3,TIM_CHANNEL_3); //关闭左右电机的 pwm 输出，防止怠速运行

}

//后退函数

void BACK(int C_COUNTER,int TIME)
{ //左电机

//HAL_TIM_PWM_Start(&htim4,TIM_CHANNEL_2);
//开启左电机的 pwm 调压

__HAL_TIM_SET_COMPARE(&htim4, TIM_CHANNEL_2, C_COUNTER); //设定左电机的占空比=C_COUNTER/1000

HAL_GPIO_WritePin(LEFT_MOTOR_GPIO | , | LEFT_MOTOR_PIN,
GPIO_PIN_SET); | /* 设定 IO 的值使左转电机正转或反转 */

//右电机

// | HAL_TIM_PWM_Start(&htim3,TIM_CHANNEL_3);
//开启右电机的 pwm 调压
__HAL_TIM_SET_COMPARE(&htim3, | | TIM_CHANNEL_3,
C_COUNTER*1.12); | //设定右电机的占空比=C_COUNTER/1000
HAL_GPIO_WritePin(RIGHT_MOTOR_GPIO, | | RIGHT_MOTOR_PIN,
GPIO_PIN_SET); | /* 设定 IO 的值使右转电机正转或反转 */
//设定运行时间

HAL_Delay(TIME);
// HAL_TIM_PWM_Stop(&htim4,TIM_CHANNEL_2);
// HAL_TIM_PWM_Stop(&htim3,TIM_CHANNEL_3); //关闭左右电机的 pwm 输出，防止怠速运行

}

//制动函数

void STOP(int C_COUNTER,int TIME)
{ | //左电机
//HAL_TIM_PWM_Start(&htim4,TIM_CHANNEL_2); | | //开启左电机的pwm调压
//HAL_TIM_PWM_Start(&htim3,TIM_CHANNEL_3); | | //开启右电机的pwm调压

38

__HAL_TIM_SET_COMPARE(&htim4, TIM_CHANNEL_2, C_COUNTER); //设定 左电机的占空比=C_COUNTER/1000
__HAL_TIM_SET_COMPARE(&htim3, TIM_CHANNEL_3, C_COUNTER); //设定 右电机的占空比=C_COUNTER/1000

HAL_Delay(TIME);
// HAL_TIM_PWM_Stop(&htim4,TIM_CHANNEL_2); //关闭左电机的 pwm 输 出，防止怠速运行
//HAL_TIM_PWM_Stop(&htim3,TIM_CHANNEL_3); //关闭右电机的 pwm 输 出，防止怠速运行

}
void left_90(int C_COUNTER_L,int C_COUNTER_R,int TIME)
{ | //左电机
//HAL_TIM_PWM_Start(&htim4,TIM_CHANNEL_2); | //开启左电机的pwm调压
//HAL_TIM_PWM_Start(&htim3,TIM_CHANNEL_3); | //开启右电机的pwm调压

HAL_GPIO_WritePin(LEFT_MOTOR_GPIO , LEFT_MOTOR_PIN, GPIO_PIN_SET); //
左轮反转 | /* 设定 IO 的值使左转电机正转 */
HAL_GPIO_WritePin(RIGHT_MOTOR_GPIO, | RIGHT_MOTOR_PIN,
GPIO_PIN_RESET); | /* 设定 IO 的值使右转电机正转 */
__HAL_TIM_SET_COMPARE(&htim4, TIM_CHANNEL_2, C_COUNTER_L); | //
设定左电机的占空比=C_COUNTER/1000

__HAL_TIM_SET_COMPARE(&htim3, TIM_CHANNEL_3, C_COUNTER_R*1.12); //设定右电机的占空比=C_COUNTER/1000

HAL_Delay(TIME);
// HAL_TIM_PWM_Stop(&htim4,TIM_CHANNEL_2); //关闭左电机的 pwm 输 出，防止怠速运行
//HAL_TIM_PWM_Stop(&htim3,TIM_CHANNEL_3); //关闭右电机的 pwm 输 出，防止怠速运行

}
void right_90(int C_COUNTER_L,int C_COUNTER_R,int TIME)
{ | //左电机
//HAL_TIM_PWM_Start(&htim4,TIM_CHANNEL_2); | //开启左电机的pwm调压
//HAL_TIM_PWM_Start(&htim3,TIM_CHANNEL_3); | //开启右电机的pwm调压

HAL_GPIO_WritePin(LEFT_MOTOR_GPIO , LEFT_MOTOR_PIN, GPIO_PIN_RESET);
//左轮反转 | /* 设定 IO 的值使左转电机正转 */
HAL_GPIO_WritePin(RIGHT_MOTOR_GPIO, | RIGHT_MOTOR_PIN,
GPIO_PIN_SET); | /* 设定 IO 的值使右转电机正转 */
__HAL_TIM_SET_COMPARE(&htim4, TIM_CHANNEL_2, C_COUNTER_L); | //
设定左电机的占空比=C_COUNTER/1000

__HAL_TIM_SET_COMPARE(&htim3, TIM_CHANNEL_3, C_COUNTER_R); //

39

设定右电机的占空比=C_COUNTER/1000

HAL_Delay(TIME);
// HAL_TIM_PWM_Stop(&htim4,TIM_CHANNEL_2); //关闭左电机的 pwm 输 出，防止怠速运行
//HAL_TIM_PWM_Stop(&htim3,TIM_CHANNEL_3); //关闭右电机的 pwm 输 出，防止怠速运行

}
void rotate_180(int C_COUNTER_L,int C_COUNTER_R,int TIME)
{ | //左电机
//HAL_TIM_PWM_Start(&htim4,TIM_CHANNEL_2); | //开启左电机的pwm调压
//HAL_TIM_PWM_Start(&htim3,TIM_CHANNEL_3); | //开启右电机的pwm调压

HAL_GPIO_WritePin(LEFT_MOTOR_GPIO , LEFT_MOTOR_PIN, GPIO_PIN_RESET);
//左轮反转 | /* 设定 IO 的值使左转电机正转 */
HAL_GPIO_WritePin(RIGHT_MOTOR_GPIO, | RIGHT_MOTOR_PIN,
GPIO_PIN_SET); | /* 设定 IO 的值使右转电机正转 */
__HAL_TIM_SET_COMPARE(&htim4, TIM_CHANNEL_2, C_COUNTER_L); | //
设定左电机的占空比=C_COUNTER/1000

__HAL_TIM_SET_COMPARE(&htim3, TIM_CHANNEL_3, C_COUNTER_R); // 设定右电机的占空比=C_COUNTER/1000

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

}

while (1)
{
/* USER CODE END WHILE */

/* USER CODE BEGIN 3 */

sprintf ((char *)str1 ,"point:%d",vechile1.Trend);

40

{
case 1:
line_follow();
if(right90_check())
{
FORWARD(500,550);
right_90(450,450,500);
right_90turn();
vechile1.Trend=2;
close_singal;
}
break;
case 2:
line_follow();
if( T_check() )
{
FORWARD(500,500);
right_90(450,450,500);
right_90turn();
vechile1.Trend=3;
}
break;
case 3:
circle_turn();
if( (right90_check() ) && (vechile1.turn_situ==0) ) {
LEFTTURN(350,675,200);//左小转

vechile1.turn_situ = 1;
}

else if( (right90_check() || T_check() ) && (vechile1.turn_situ==1) ) {
RIGHTTURN(520,450,650);
right_90(450,450,650);
right_90turn();
vechile1.turn_situ = 0;
vechile1.Trend=4;
//line_follow();
}

41

break;
case 4: //进到第一个路口抓物块

line_follow();
if( left90_check() )
| { FORWARD(500,530); left_90(450,450,300); left_90turn(); vechile1.Trend=16; } break;

case 16:
line_follow_slowdown();
if( T_check() )
{
| STOP(0,500); send_singal; STOP(0,1500); close_singal; vechile1.Trend=5;

}
break;
case 5:
BACK(350,2600);
left_90(450,450,650);
left_90turn();
vechile1.Trend=7;
break;
case 7:
line_follow();
if( T_check() )
{
| FORWARD(500,540); right_90(450,450,2); right_90turn(); vechile1.Trend=8;

}
break;
case 8:

42

circle_turn();
if( (right90_check() ) && (vechile1.turn_situ==0) ) {
LEFTTURN(350,670,150);//左小转

vechile1.turn_situ = 1;
}
if( (right90_check() || T_check() ) && (vechile1.turn_situ==1) ) {
RIGHTTURN(520,450,650);
right_90(450,450,650);
right_90turn();
vechile1.turn_situ = 0;
vechile1.Trend=9;
}
break;

case 9:
line_follow();
if( left90_check() )
{
FORWARD(500,520);
left_90(450,450,500);
left_90turn();
vechile1.Trend=10;
}
break;
case 10:
line_follow();
if( T_check() )
{
STOP(0,500);
send_singal;
STOP(0,1500);
close_singal;
vechile1.Trend=11;
}
break;
case 11:
BACK(350,500);

43

if( right_180turn() )
{
}
break;

case 13:
line_follow();
if( T_check() )
{
FORWARD(500,500);
left_90(450,450,500);
left_90turn();
vechile1.Trend=14;
}
break;
case 14:
line_follow();
if(left90_check())
{
FORWARD(500,530);
left_90(450,450,500);
left_90turn();
vechile1.Trend=15;
}
case 15:
line_follow();
if( T_check() )
{
STOP(0,500);
}
break;
}
}
/* USER CODE END 3 */
}

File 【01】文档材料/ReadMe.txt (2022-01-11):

1、Word类放入可编辑类文档，如word或wps文档。
2、PDF类放入word类文档另存为pdf文件，避免因为word公式乱码等问题发生。

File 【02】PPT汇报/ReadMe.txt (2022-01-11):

该文件夹放入所有历次汇报PPT文档，如PPT中有视频类文件，请放入【补充材料】文件夹中。

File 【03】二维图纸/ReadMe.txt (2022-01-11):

【CAD格式】文件中放入所有绘制的二维图纸（AutoCAD或CAXA）
同时将CAD格式图纸另存为或虚拟打印出PDF格式后存入【PDF格式】文件夹中。

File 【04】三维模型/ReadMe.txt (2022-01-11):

将所有绘制的三维模型放入上述文件夹中，同时将其名称保存为“软件名称+版本号”，如SolidWorks2016a。

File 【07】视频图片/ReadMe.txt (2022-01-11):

将视频和图片分别放入对应文件夹中，内容不仅限于日常工作照片、成果展示、团队合影等。

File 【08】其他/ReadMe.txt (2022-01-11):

如有其他补充请放入该文件夹。

星火相传，代代出新，2021感谢相遇，2022依旧在一起。

机电实验室 丰宗强 18713502217，如有问题，请随时与我联系！

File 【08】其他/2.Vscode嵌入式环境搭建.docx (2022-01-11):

Vscode+PlatformIO环境搭建

参考资料：https://www.bilibili.com/video/BV1tv411w74d?from=search&seid=10236622600450991913&spm_id_from=333.337.0.0

1. 安装完vscode
2. 在左上角最后一个拓展选项(Extention)中直接搜索Chinese,安装中文语言包，重启vscode


3. 仍在拓展中搜索PlatformIO IDE，安装该插件，会自动下载其附带的C/C++，Cmake拓展包（建议提前把默认保存途径换到其他盘）。


4. 在PIO 中点击Open，进入主页面。主页面四选项分别为：创建工程；导入工程；打开工程；工程实例。此处直接建立新工程即可。


5. 创建工程，需按下图设置，如果ESP32开发板型号为基础版，直接按下图设置即可，框架可选Arduino框架或Expressif官方框架。创建文件后会自动下载开发板的框架包，可以在网络良好处等待一段时间。


6. 在main.cpp文件中编写控制程序即可。
7. ESP32基于Arduino框架的定时器设置、中断、串口使用及其他功能请参考文首视频或太极创客Arduino教程。

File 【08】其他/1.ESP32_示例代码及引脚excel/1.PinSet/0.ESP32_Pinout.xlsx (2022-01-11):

IO选择 | 对应功能 | IO编号 | 启动项相关 | ADC | DAC | UART | Touch | SPI/IIC
 |  | GPIO0 | 下载：低电平/启动：高电平 | ADC2_1 |  |  | TP_1
 |  | GPIO1 |  |  |  | TX0
 |  | GPIO2 |  | ADC2_2 |  |  | TP_2
 |  | GPIO3 |  |  |  | RX0
 |  | GPIO4 |  | ADC2_0 |  |  | TP_0
 |  | GPIO5 | 启动时必须高电平 |  |  |  |  | VSPI
 |  | GPIO6 | 连接了FLASH(CLK)
 |  | GPIO7 | 连接了FLASH(SD0)
 |  | GPIO8 | 连接了FLASH(SD1)
 |  | GPIO9 | 连接了FLASH(SD2) |  |  | RX1
 |  | GPIO10 | 连接了FLASH(SD3) |  |  | TX1
 |  | GPIO11 | 连接了FLASH(CMD)
 |  | GPIO12 | 启动时必须低电平 | ADC2_5 |  |  | TP_5 | HSPI
 |  | GPIO13 |  | ADC2_4 |  |  | TP_4 | HSPI
 |  | GPIO14 | 启动时必须高电平 | ADC2_6 |  |  | TP_6 | HSPI
 |  | GPIO15 | 启动时必须高电平 | ADC2_3 |  |  | TP_3 | HSPI
 |  | GPIO16 |  |  |  | RX2
 |  | GPIO17 |  |  |  | TX2
 |  | GPIO18 |  |  |  |  |  | VSPI
 |  | GPIO19 |  |  |  |  |  | VSPI
 |  | GPIO21 |  |  |  |  |  | IIC_SDA
 |  | GPIO22 |  |  |  |  |  | IIC_SCL
 |  | GPIO23 |  |  |  |  |  | VSPI
 |  | GPIO25 |  | ADC2_8 | DAC_1
 |  | GPIO26 |  | ADC2_9 | DAC_2
 |  | GPIO27 |  | ADC2_7 |  |  | TP_7
 |  | GPIO32 |  | ADC1_4 |  |  | TP_9
 |  | GPIO33 |  | ADC1_5 |  |  | TP_8
 |  | GPIO34 | Input Only | ADC1_6
 |  | GPIO35 | Input Only | ADC1_7
 |  | GPIO36 | Input Only/SVP | ADC1_0
 |  | GPIO39 | Input Only/SVN | ADC1_3
说明： 1. 使用Wi-Fi会与ADC2冲突，要注意！ 2. ADC的使用并非线性的，0-0.1V和3.2-3.3V区间就是有问题的！

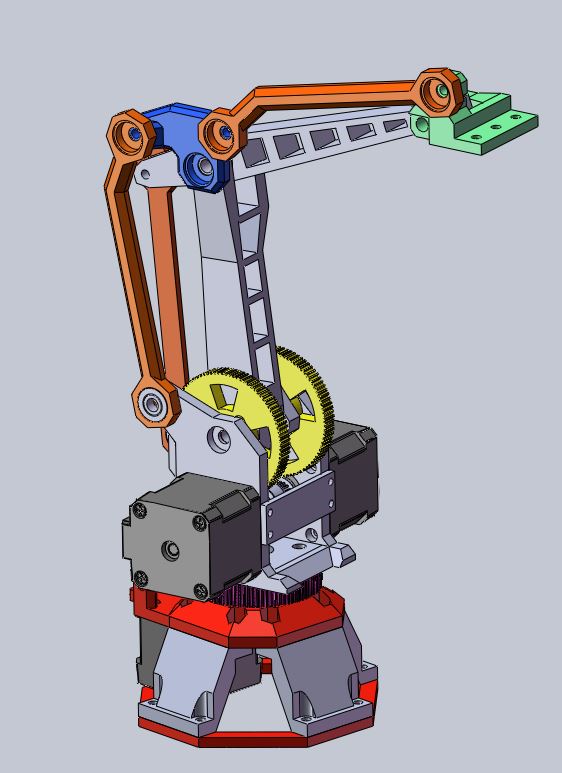
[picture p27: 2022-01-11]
【04】三维模型/SOLIDWORKS-2018/履带车/机械手/机械手1.JPG

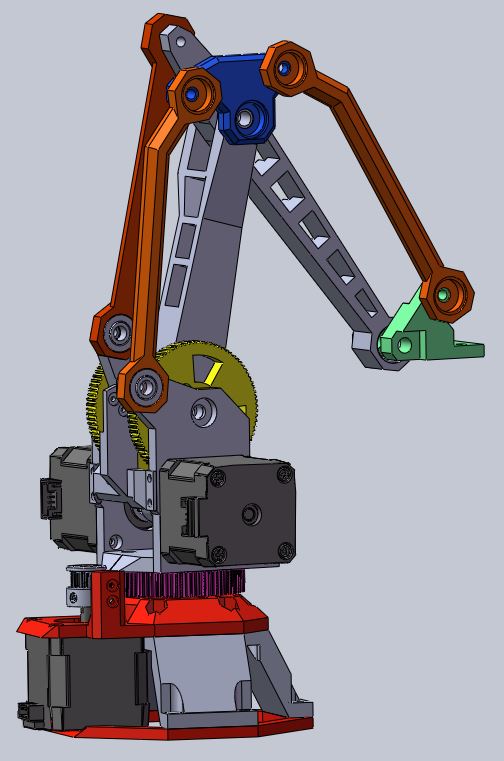
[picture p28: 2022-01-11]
【04】三维模型/SOLIDWORKS-2018/履带车/机械手/机械手2.JPG

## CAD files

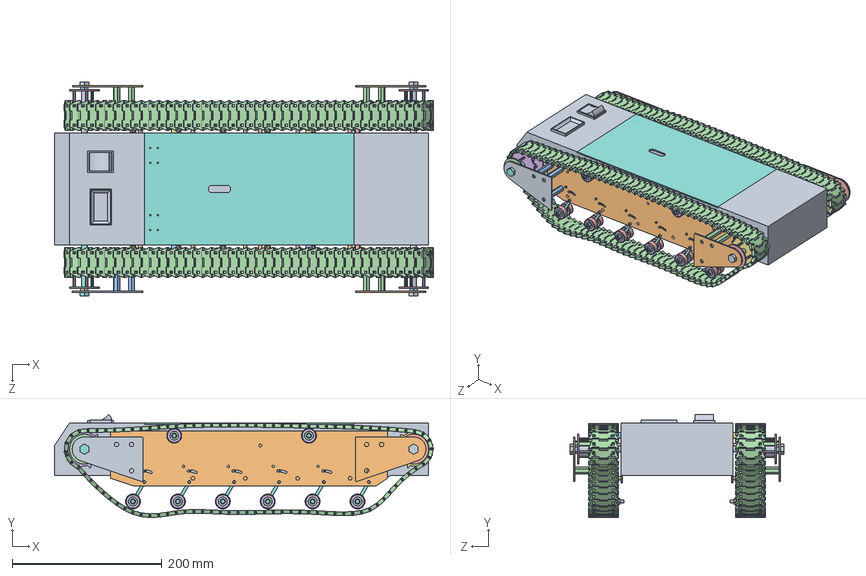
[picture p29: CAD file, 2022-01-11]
【04】三维模型/SOLIDWORKS-2018/履带车/履带/履带车.SLDASM
506.4 x 137.9 x 286.0 mm
车体
板子
下螺栓 x 8
轴承内圈 x 16
轴承外圈 x 16
轴承中圈 x 16
下部螺母 x 22
下部连接 x 6
螺栓3M x 6
铜柱 x 8
铜柱8M x 2
外侧圆板
齿铜柱 x 6
齿 x 2
齿内测铜柱
传动轮螺栓
最外侧支撑板
8M螺母 x 2
43铜柱 x 3
M2螺栓 x 12
镜向外侧圆板 x 2
镜向齿铜柱 x 12
镜向齿 x 4
镜向齿内测铜柱 x 2
镜向传动轮螺栓 x 2
镜向最外侧支撑板 x 2
镜向8M螺母 x 4
镜向43铜柱 x 6
镜向镜向外侧圆板
镜向镜向齿铜柱 x 6
镜向镜向齿 x 2
镜向镜向齿内测铜柱
镜向镜向传动轮螺栓
镜向镜向最外侧支撑板
镜向镜向8M螺母 x 2
镜向镜向43铜柱 x 3
镜向板子
镜向下螺栓 x 8
镜向轴承内圈 x 16
镜向轴承外圈 x 16
镜向轴承中圈 x 16
镜向下部螺母 x 22
镜向下部连接 x 6
镜向螺栓3M x 6
镜向铜柱 x 8
镜向M2螺栓 x 11
镜向铜柱8M x 2
上盖
按钮
弹簧 x 12
M3螺母 x 12
履带齿 x 183

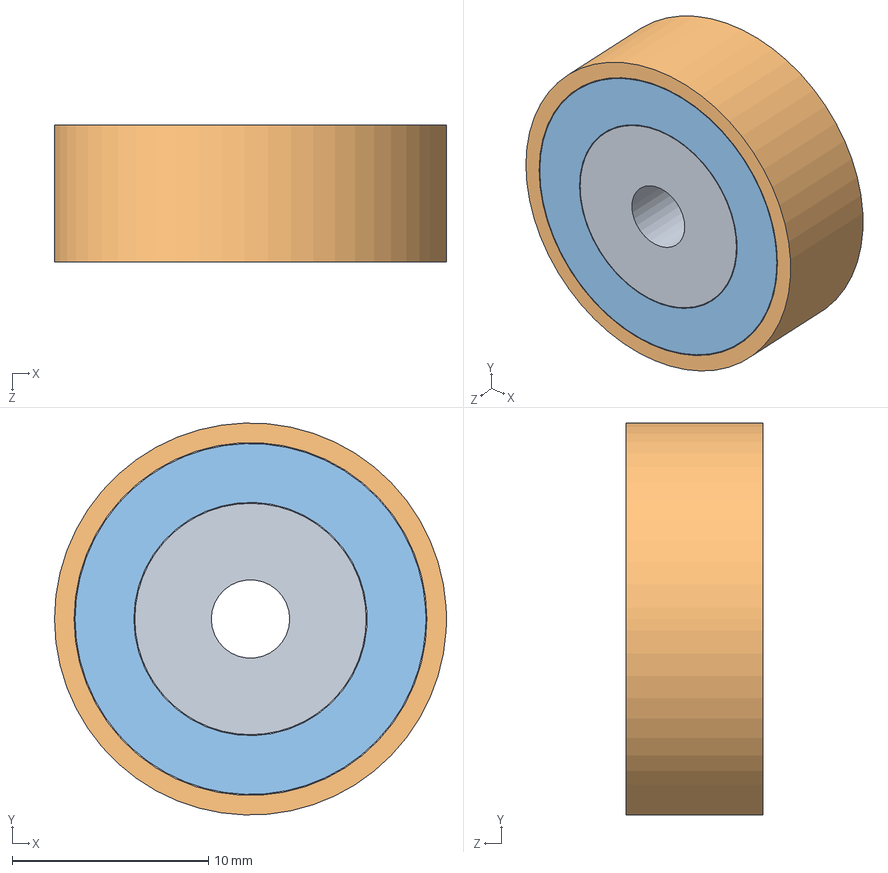
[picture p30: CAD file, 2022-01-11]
【04】三维模型/SOLIDWORKS-2018/履带车/履带/轴承/轴承.SLDASM
20.0 x 20.0 x 7.00 mm
轴承内圈
轴承外圈
轴承中圈

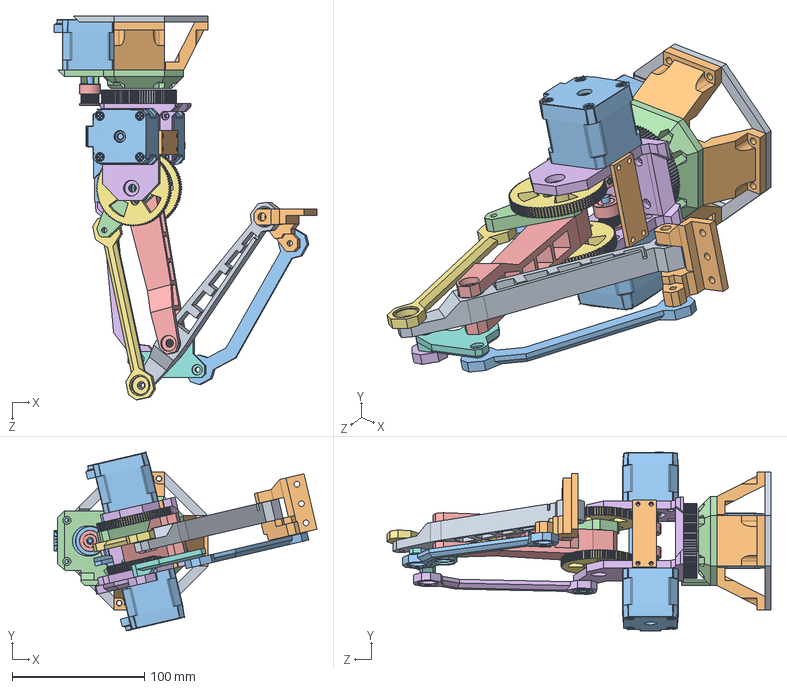
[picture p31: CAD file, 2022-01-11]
【04】三维模型/SOLIDWORKS-2018/履带车/机械手/机械手.SLDASM
198.6 x 134.9 x 289.6 mm
基座底板
基座支架 x 3
基座电机 x 3
基座顶板
基座小带轮 x 3
支架
机械臂大带轮 x 2
机械臂大带轮轴承 x 8
基座大带轮
支架横板
支架挡板
大臂连杆
大臂杆2
大臂杆3
大臂杆1
三连杆
小臂杆2
小臂连杆
小臂杆1

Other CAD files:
【04】三维模型/SOLIDWORKS-2018/履带车/履带/轴承/镜向轴承12.SLDASM
【04】三维模型/SOLIDWORKS-2018/履带车/履带/轴承/镜向轴承2.SLDASM
【04】三维模型/SOLIDWORKS-2018/履带车/履带/轴承/镜向轴承10.SLDASM
【04】三维模型/SOLIDWORKS-2018/履带车/履带/轴承/镜向轴承15.SLDASM
【04】三维模型/SOLIDWORKS-2018/履带车/履带/轴承/镜向轴承6.SLDASM
【04】三维模型/SOLIDWORKS-2018/履带车/履带/轴承/镜向轴承8.SLDASM
【04】三维模型/SOLIDWORKS-2018/履带车/履带/镜向镜向传动轮.SLDASM
【04】三维模型/SOLIDWORKS-2018/履带车/履带/轴承/镜向轴承7.SLDASM
【04】三维模型/SOLIDWORKS-2018/履带车/履带/镜向下导轮5.SLDASM
【04】三维模型/SOLIDWORKS-2018/履带车/履带/轴承/镜向轴承14.SLDASM
【04】三维模型/SOLIDWORKS-2018/履带车/履带/轴承/镜向轴承9.SLDASM
【04】三维模型/SOLIDWORKS-2018/履带车/履带/轴承/镜向轴承.SLDASM
【04】三维模型/SOLIDWORKS-2018/履带车/履带/轴承/镜向轴承5.SLDASM
【04】三维模型/SOLIDWORKS-2018/履带车/履带/轴承/镜向轴承13.SLDASM
【04】三维模型/SOLIDWORKS-2018/履带车/履带/轴承/镜向轴承11.SLDASM
【04】三维模型/SOLIDWORKS-2018/履带车/M3螺母.SLDPRT
【04】三维模型/SOLIDWORKS-2018/履带车/履带/16圆柱.SLDPRT
【04】三维模型/SOLIDWORKS-2018/履带车/履带/43铜柱.SLDPRT
【04】三维模型/SOLIDWORKS-2018/履带车/履带/8M螺母.SLDPRT
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

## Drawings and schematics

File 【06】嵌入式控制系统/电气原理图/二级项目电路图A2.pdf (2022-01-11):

# 系统供电接口 四路红外循迹

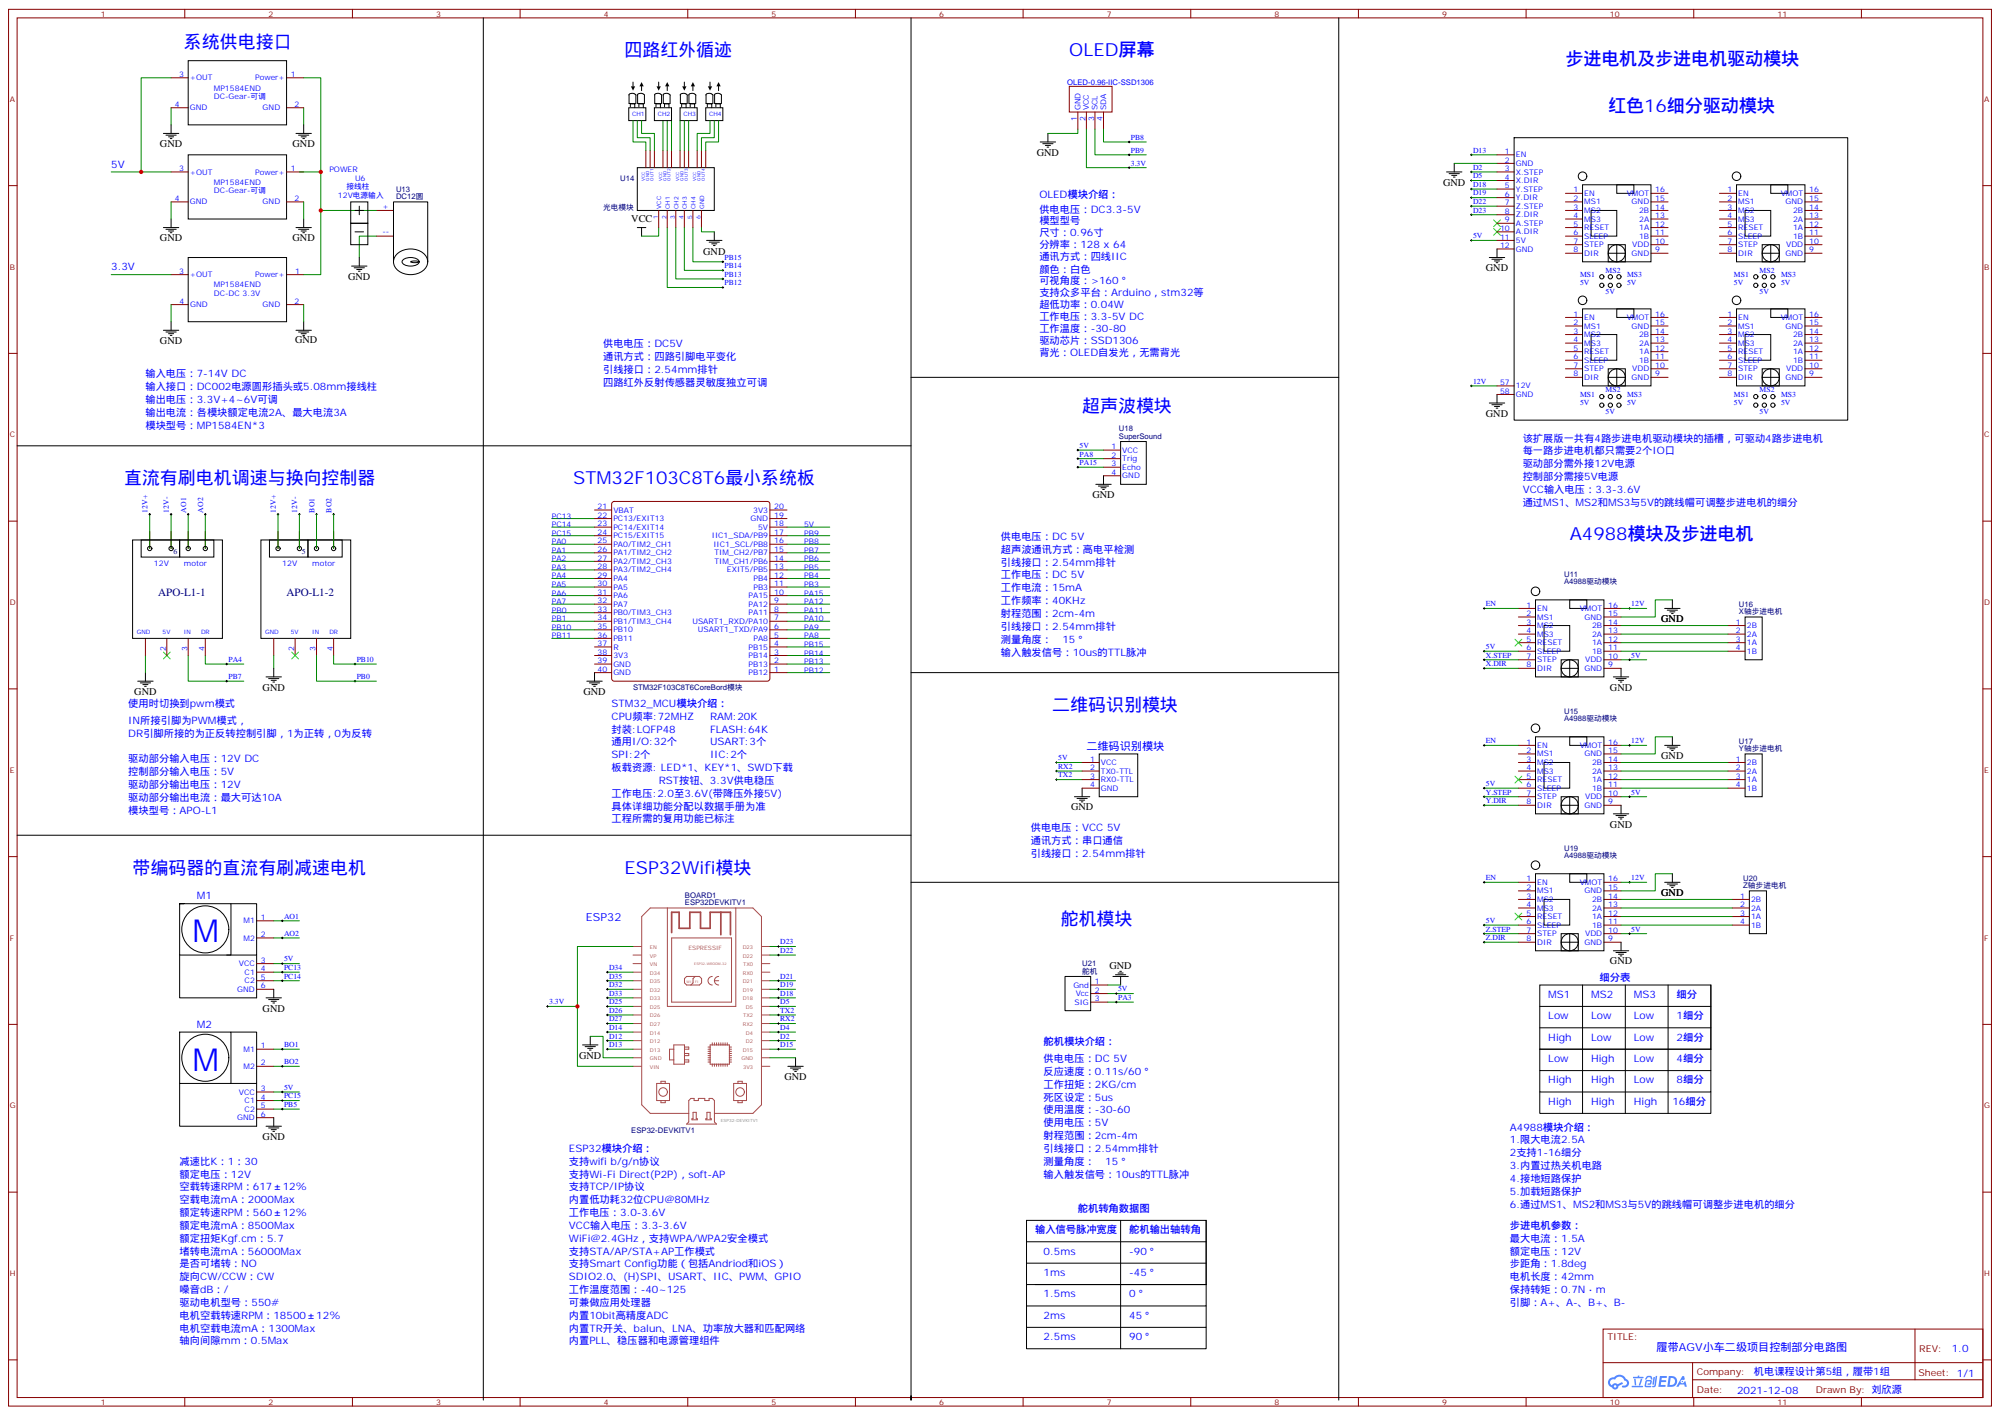
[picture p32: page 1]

SDA 4 SCL 3 VCC 2 GND 1

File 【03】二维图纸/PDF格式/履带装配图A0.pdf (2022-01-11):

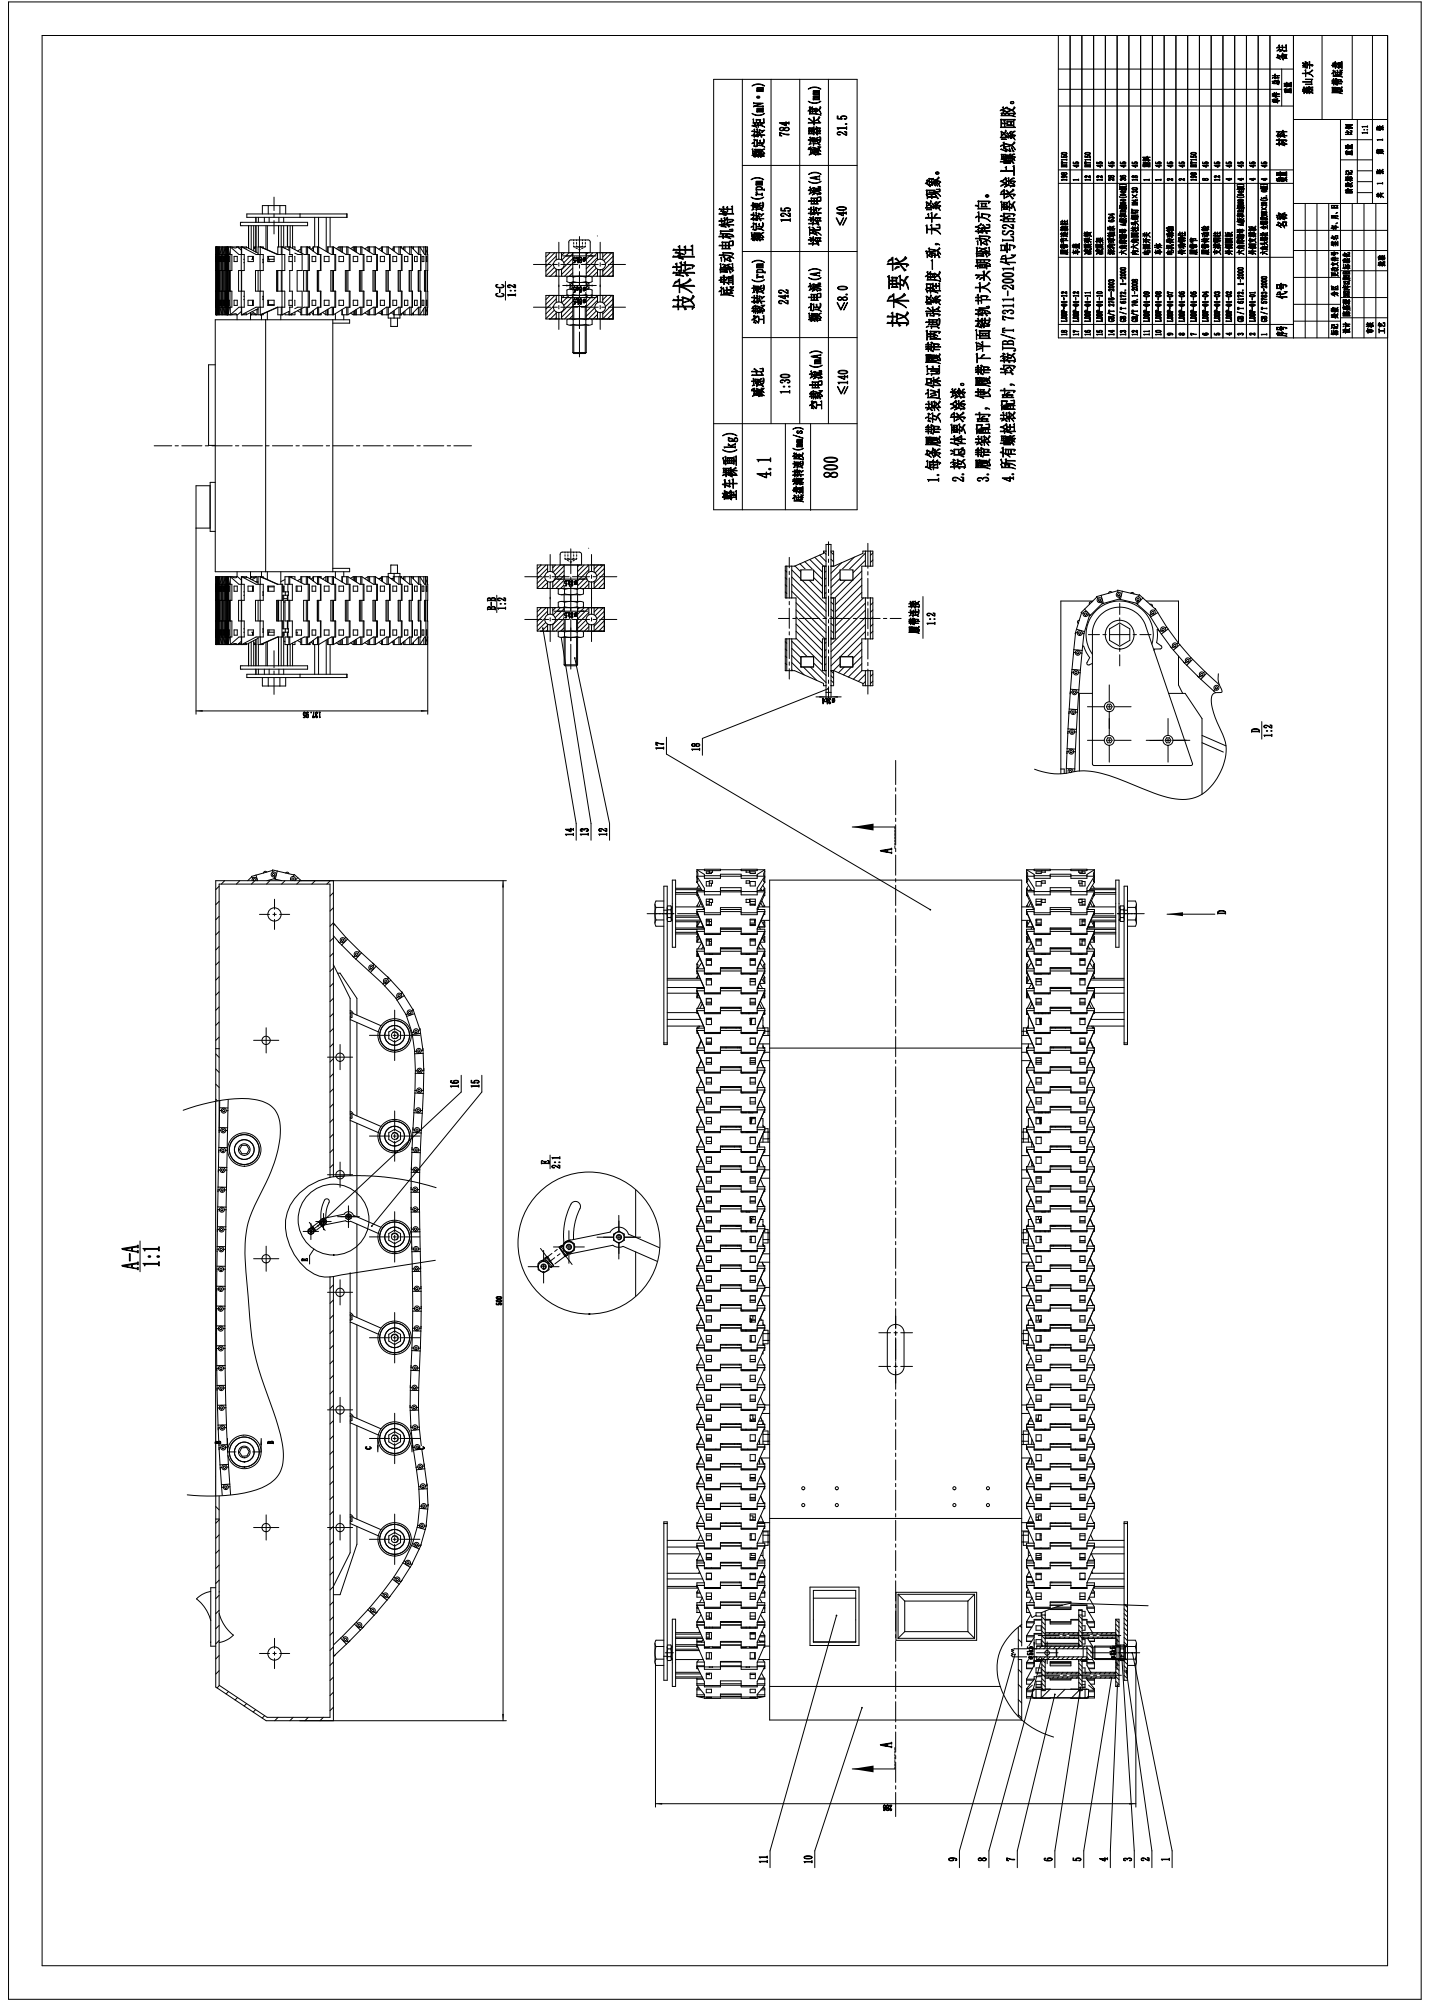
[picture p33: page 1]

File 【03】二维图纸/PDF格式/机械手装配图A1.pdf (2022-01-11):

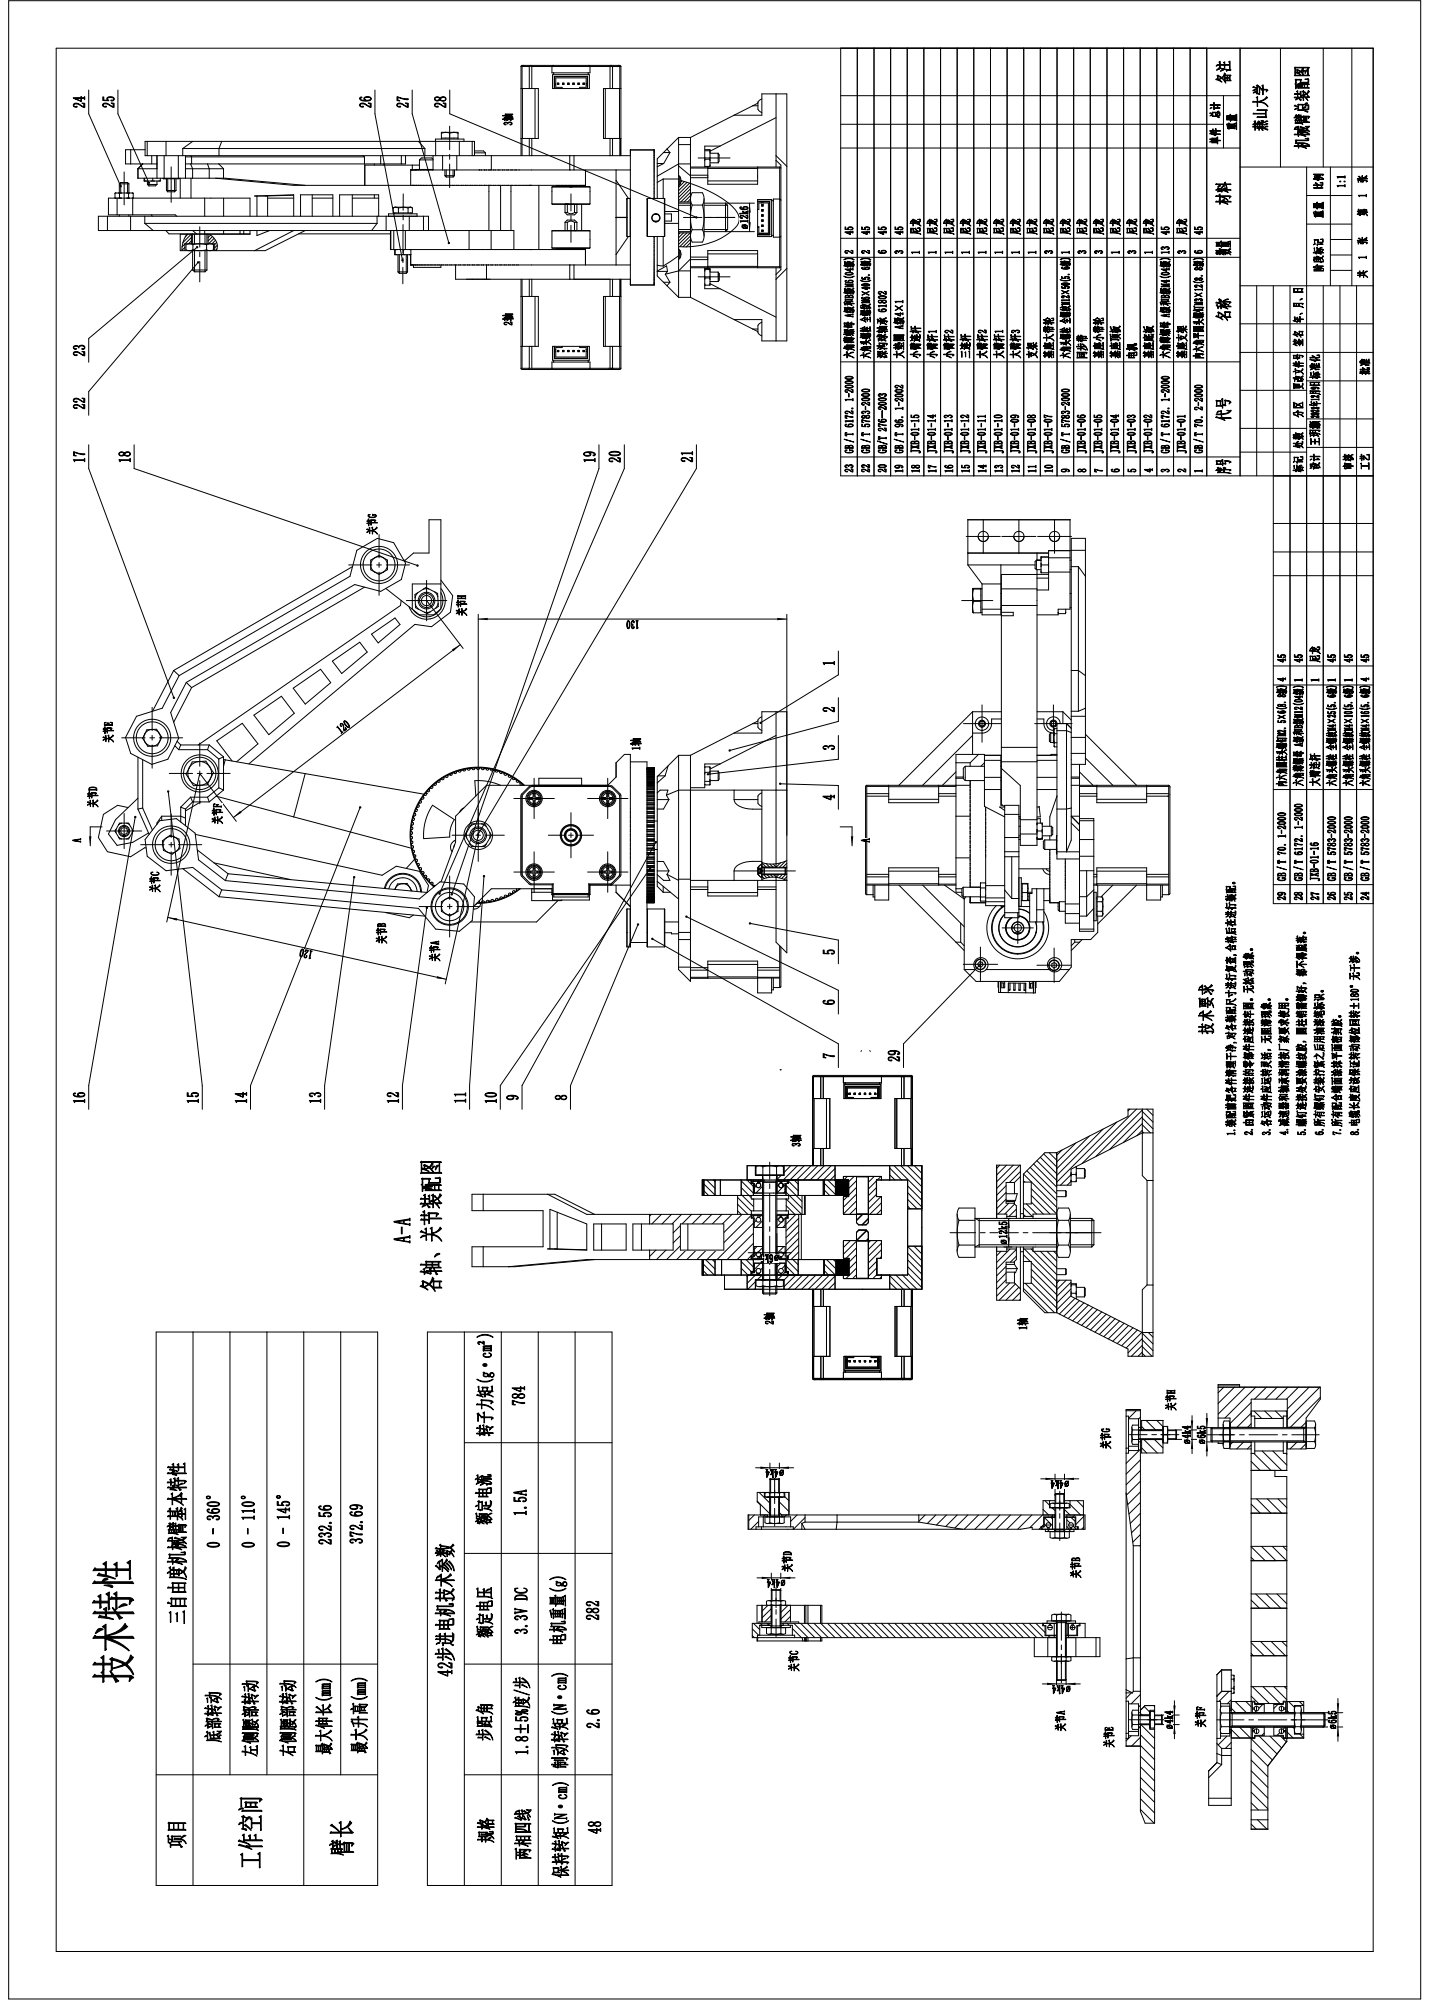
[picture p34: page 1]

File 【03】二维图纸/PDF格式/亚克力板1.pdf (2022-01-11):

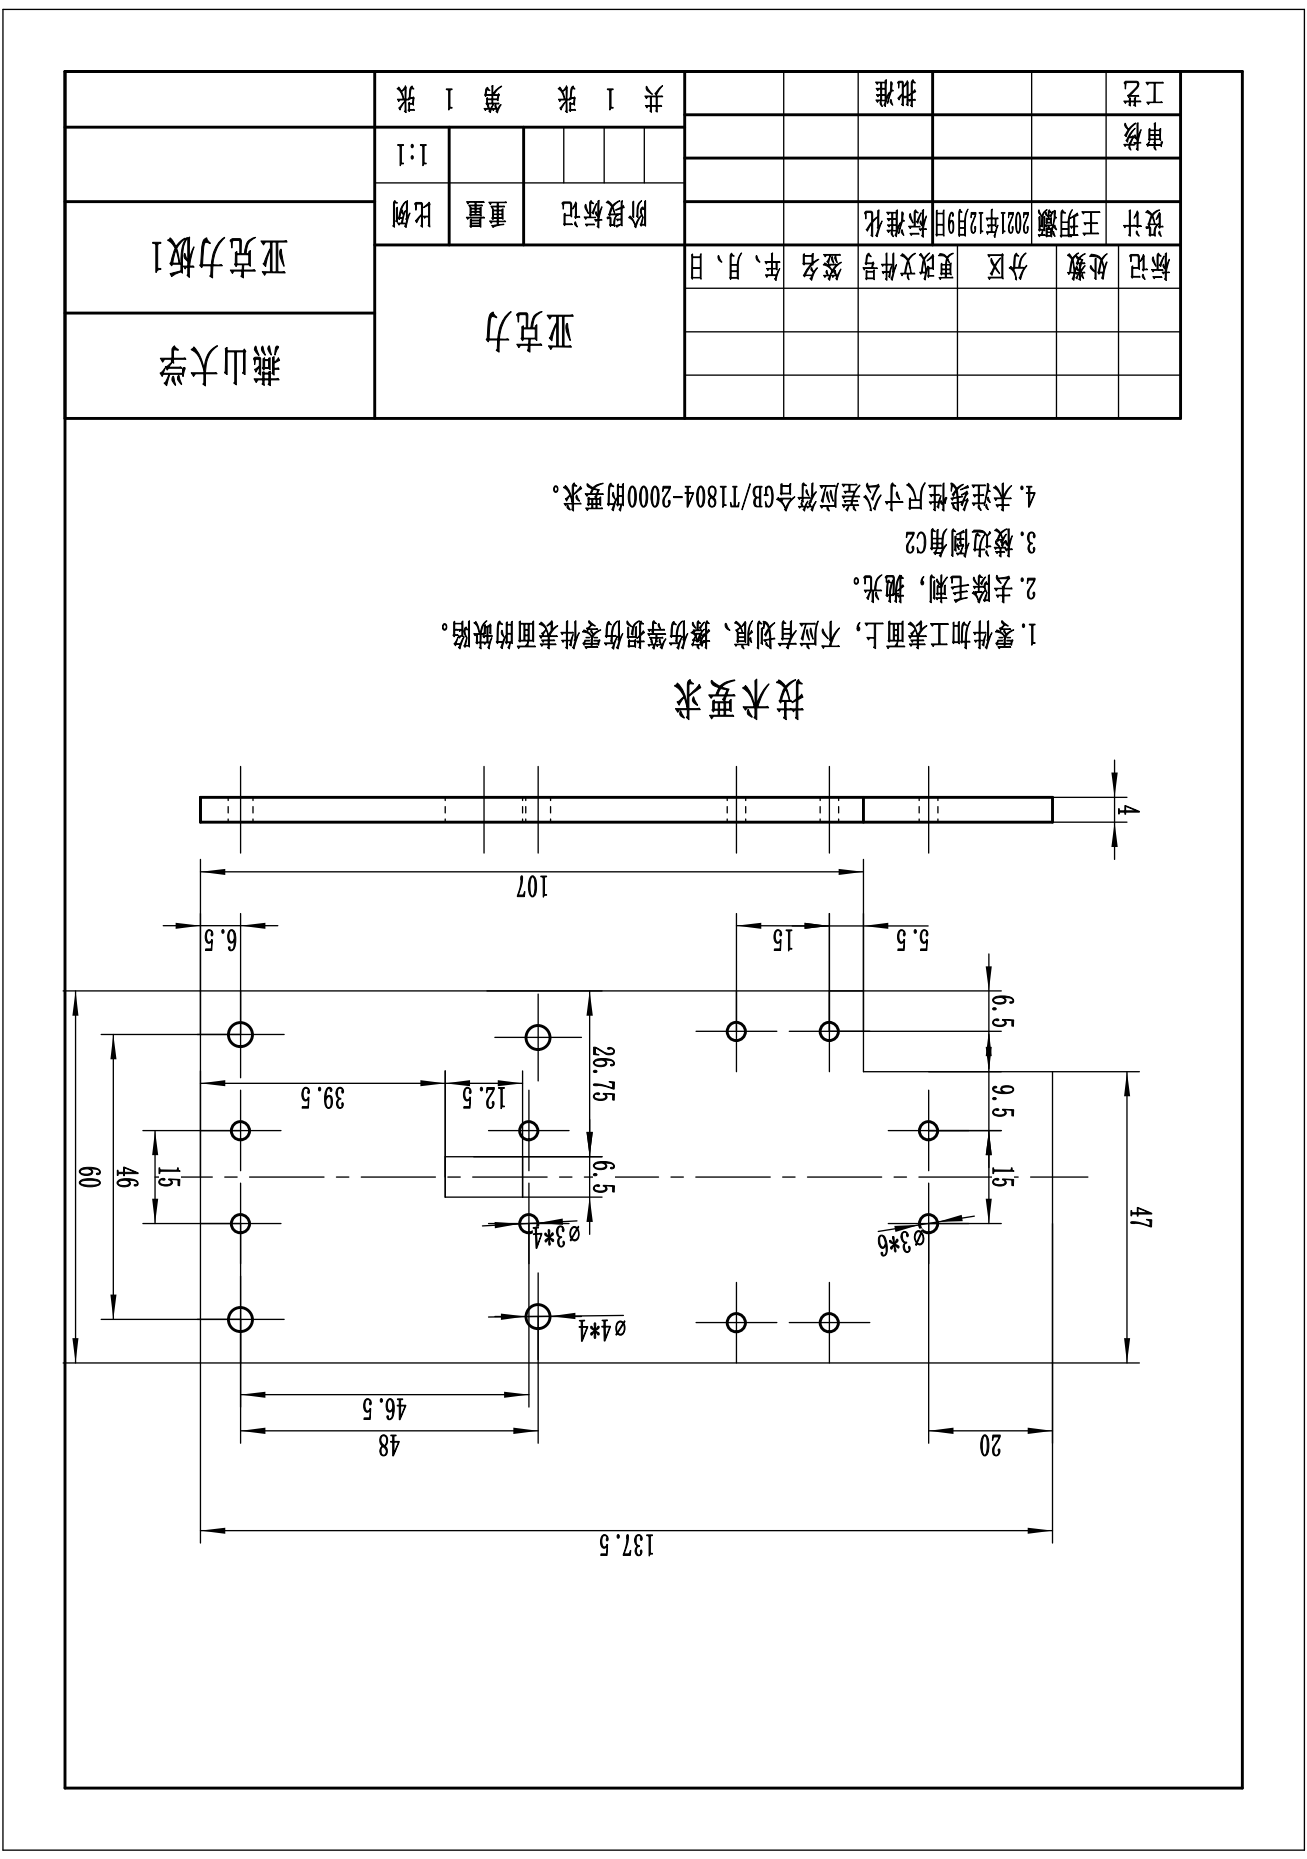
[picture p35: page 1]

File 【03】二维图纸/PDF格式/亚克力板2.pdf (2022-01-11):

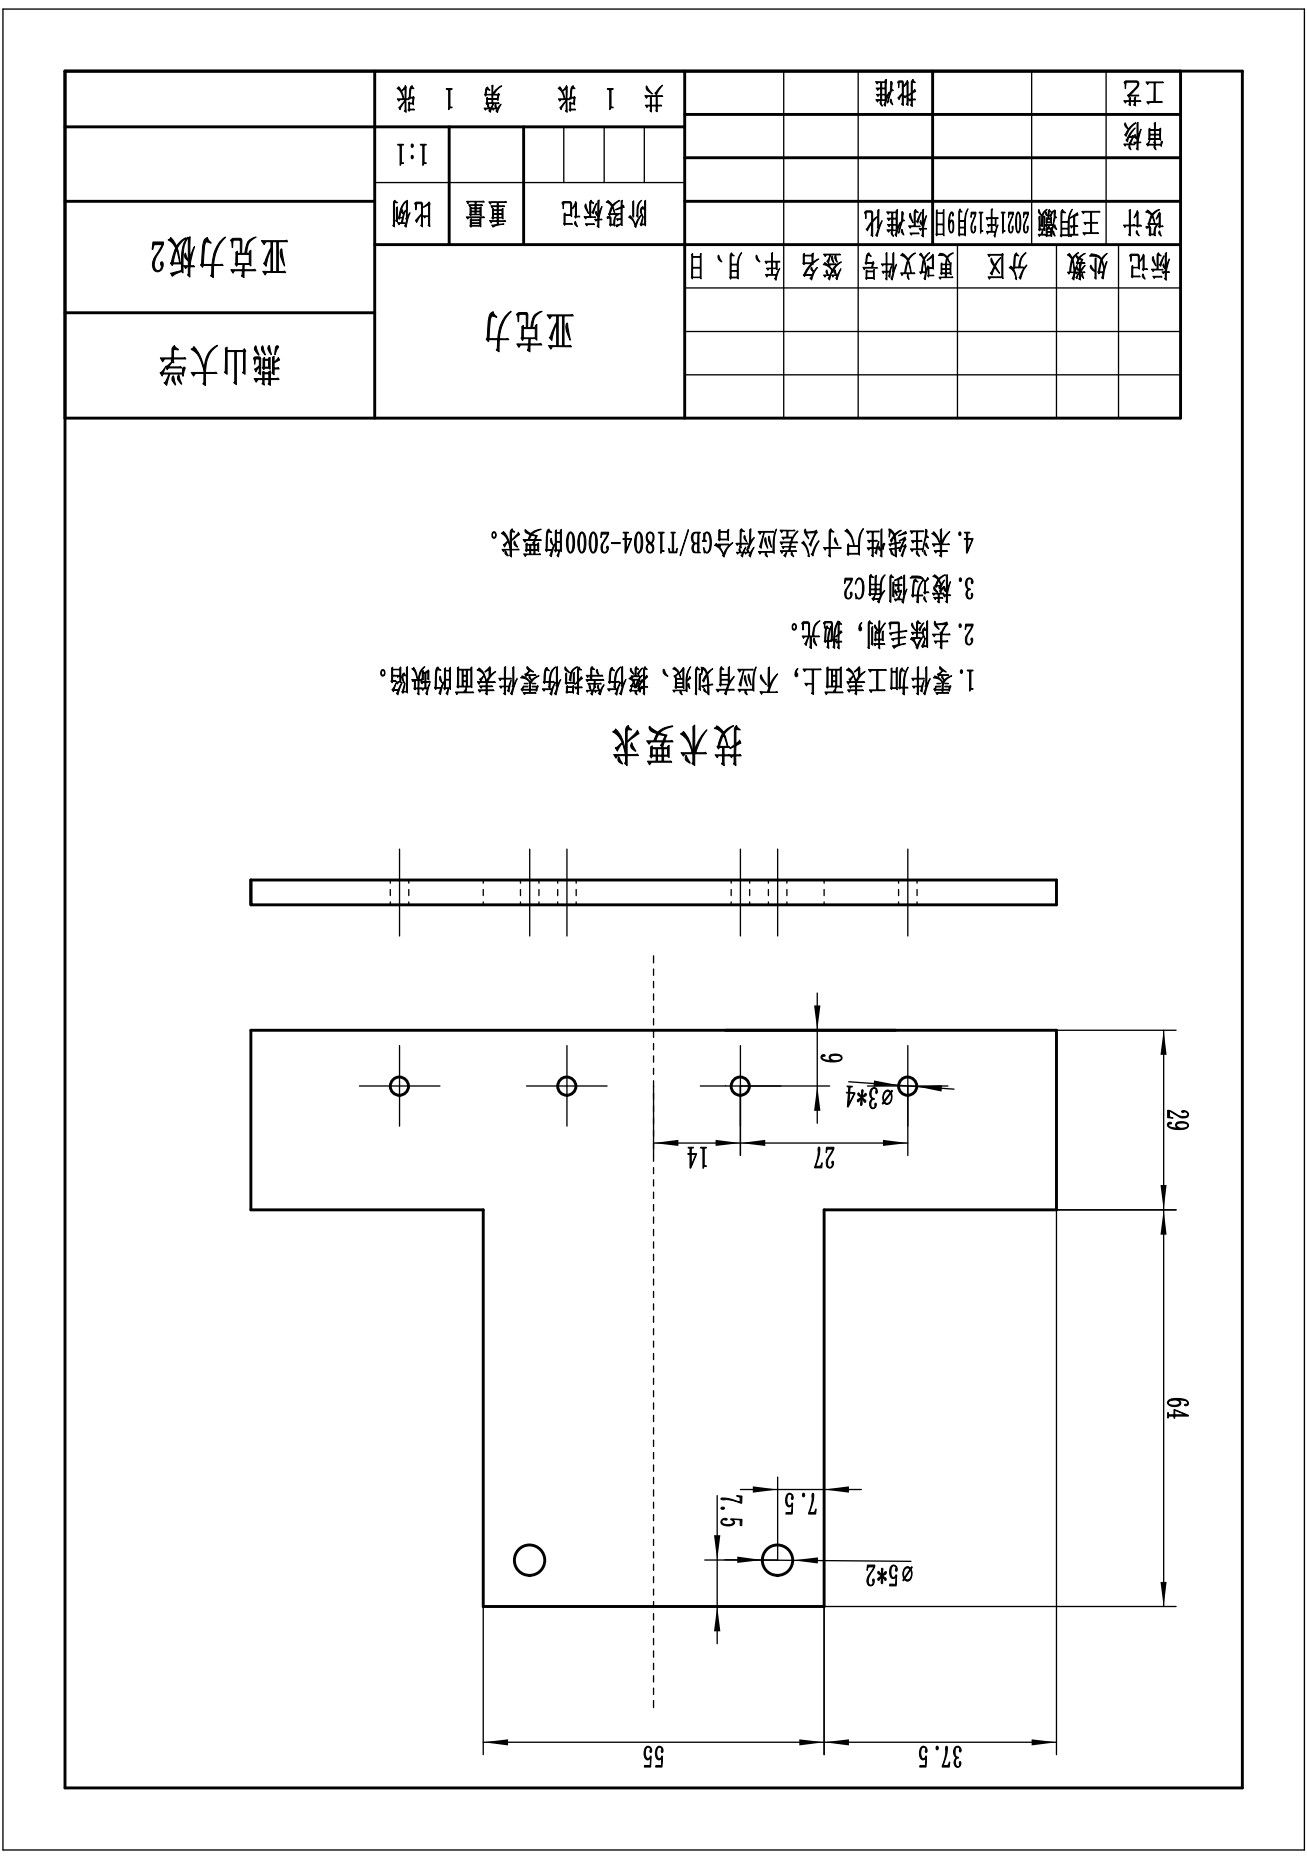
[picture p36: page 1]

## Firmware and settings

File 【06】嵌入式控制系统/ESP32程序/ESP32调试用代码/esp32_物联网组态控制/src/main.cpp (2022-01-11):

#include <Arduino.h>

/* *****************************************************************

   Download latest Blinker library here:
   https://github.com/blinker-iot/blinker-library/archive/master.zip


   Blinker is a cross-hardware, cross-platform solution for the IoT.
   It provides APP, device and server support,
   and uses public cloud services for data transmission and storage.
   It can be used in smart home, data monitoring and other fields
   to help users build Internet of Things projects better and faster.

   Make sure installed 2.7.4 or later ESP8266/Arduino package,
   if use ESP8266 with Blinker.
   https://github.com/esp8266/Arduino/releases

   Make sure installed 1.0.5 or later ESP32/Arduino package,
   if use ESP32 with Blinker.
   https://github.com/espressif/arduino-esp32/releases

   Docs: https://diandeng.tech/doc


 * *****************************************************************

   Blinker 库下载地址:
   https://github.com/blinker-iot/blinker-library/archive/master.zip

   Blinker 是一套跨硬件、跨平台的物联网解决方案，提供APP端、设备端、
   服务器端支持，使用公有云服务进行数据传输存储。可用于智能家居、
   数据监测等领域，可以帮助用户更好更快地搭建物联网项目。

   如果使用 ESP8266 接入 Blinker,
   请确保安装了 2.7.4 或更新的 ESP8266/Arduino 支持包。
   https://github.com/esp8266/Arduino/releases

   如果使用 ESP32 接入 Blinker,
   请确保安装了 1.0.5 或更新的 ESP32/Arduino 支持包。
   https://github.com/espressif/arduino-esp32/releases

   文档: https://diandeng.tech/doc


 * *****************************************************************/



//#define BLINKER_BLE  
#define BLINKER_WIFI
#define LED_BUILTIN 2

#define outpin 4
#define getinpin1 35

#include <../lib/Blinker/src/Blinker.h>
#include <../lib/stepset.h>
#include <../lib/AccelStepper/src/AccelStepper.h>
#include <Servo.h>

char auth[] = "2fa0d2a306bf";
char ssid[] = "konodioda";
char pswd[] = "23333333";


Servo myservo;  // create servo object to control a servo 
                // a maximum of eight servo objects can be created 

// 新建组件对象
BlinkerButton Button1( (char*)"key1" );
BlinkerButton Buttonre0( (char*)"btn-0" );

BlinkerNumber Num1( (char*)"num-1" );
BlinkerNumber Num_D1( (char*)"num-D1" );
BlinkerNumber Num_D2( (char*)"num-D2" );
BlinkerNumber Num_D3( (char*)"num-D3" );

// BlinkerSlider bar1( (char*)"bar1" );
// BlinkerSlider bar2( (char*)"bar2" );
// BlinkerSlider bar3( (char*)"bar3" );

int16_t D1=0;int16_t D2=0;int16_t D3=0;
int16_t getbig_deg1[2] = {-26,26};
int16_t getbig_deg2[2] = {47,107};
int16_t getbig_deg3[2] = {11,11};


int16_t getsmall_deg1[2] = {23,23};
int16_t getsmall_deg2[2] = {52,107};
int16_t getsmall_deg3[2] = {11,11};

int16_t savebig1_deg1[2] = {120,191};
int16_t savebig1_deg2[2] = {10,39};
int16_t savebig1_deg3[2] = {40,27};
//int16_t savebig2_deg1;int16_t savebig2_deg2;int16_t savebig2_deg3;
int16_t savesmall1_deg1[2] = {160,208};
int16_t savesmall1_deg2[2] = {0,24};
int16_t savesmall1_deg3[2] = {40,19};
//int16_t savesmall2_deg1;int16_t  savesmall2_deg2;int16_t  savesmall2_deg3;
int16_t put_deg1[2] = {90,0};
int16_t put_deg2[2] = {20,59};
int16_t put_deg3[2] = {30,23};

bool  button_on_flag=0;
bool  button_re0_flag=0;
uint8_t roboflag=1;
//char state_axis[]="";


// 按下按键即会执行该函数
void button1_callback(const String & state)
{
    if (state=="on") {
        //digitalWrite(LED_BUILTIN, HIGH);
        // 反馈开关状态
        
        button_on_flag=1;
        Button1.print("on");
        digitalWrite(outpin,HIGH);
        
    } else if(state=="off"){
        //digitalWrite(LED_BUILTIN, LOW);
        // 反馈开关状态
        //Blinker.vibrate();
        button_on_flag=0;
        Button1.print("off");
    }
    
}
void buttonre0_callback(const String & state)
{
  button_re0_flag=1;
}


void setup()
{
 //Blinker.begin();
  Serial.begin(115200);
  Blinker.begin(auth, ssid, pswd);
  
  // Blinker.connect();
  // delay(1000);

  // 初始化有LED的IO
  pinMode(LED_BUILTIN, OUTPUT);
  pinMode(outpin, OUTPUT);
  pinMode(getinpin1, INPUT);

  digitalWrite(LED_BUILTIN, LOW);
  digitalWrite(outpin, LOW);
  // 初始化blinker
  Motor_Setup();

  Button1.attach(button1_callback);
  Buttonre0.attach(buttonre0_callback);

  myservo.attach(18);  // attaches the servo on pin 9 to the servo object 
  myservo.write(78);
}

void loop() {
  Blinker.run();
  if(digitalRead(getinpin1)==1){
    switch (roboflag)
    {
    case 1:
      while(digitalRead(getinpin1)==1)
      {
        digitalWrite(LED_BUILTIN,HIGH);
        Blinker.run();
      }
      Num_D1.print(2);
      Num_D2.print(0);
      Num_D3.print(2);
      roboflag++;
      digitalWrite(LED_BUILTIN,LOW);
      break;

    case 2://取用物块

      while(digitalRead(getinpin1)==1)
      {
        digitalWrite(LED_BUILTIN,HIGH);
        //抓放大底盘
        motor_run(getbig_deg1[0],getbig_deg2[0],getbig_deg3[0]);//抓大底盘
        delay(500);
        motor_run(getbig_deg1[1],getbig_deg2[1],getbig_deg3[1]);//抓大底盘
        delay(500);
        myservo.write(37);
        delay(500);
        motor_run(savebig1_deg1[0],savebig1_deg2[0],savebig1_deg3[0]);//放大底盘
        delay(500);
        motor_run(savebig1_deg1[1],savebig1_deg2[1],savebig1_deg3[1]);//放大底盘
        delay(500);
        myservo.write(78);
        delay(500);

        //抓放小物块
        motor_run(getsmall_deg1[0],getsmall_deg2[0],getsmall_deg3[0]);//抓大底盘
        delay(500);
        motor_run(getsmall_deg1[1],getsmall_deg2[1],getsmall_deg3[1]);//抓大底盘
        delay(500);
        myservo.write(0);
        delay(500);
        motor_run(savesmall1_deg1[0],savesmall1_deg2[0],savesmall1_deg3[0]);//放大底盘
        delay(500);
        motor_run(savesmall1_deg1[1],savesmall1_deg2[1],savesmall1_deg3[1]);//放大底盘
        delay(500);
        myservo.write(78);
        delay(500);

        //
      }
      roboflag++;
      digitalWrite(LED_BUILTIN,LOW);
      break;

      case 3://放回物块

      while(digitalRead(getinpin1)==1)
      {
        //抓放小物块
        motor_run(getsmall_deg1[0],getsmall_deg2[0],getsmall_deg3[0]);//抓小物块
        delay(500);
        motor_run(getsmall_deg1[1],getsmall_deg2[1],getsmall_deg3[1]);//抓小物块
        delay(500);
        myservo.write(80);
        delay(500);
        motor_run(put_deg1[0],put_deg2[0],put_deg3[0]);//放小物块
        delay(500);
        motor_run(put_deg1[1],put_deg2[1],put_deg3[1]);//放小物块
        delay(500);
        myservo.write(0);
        delay(500);


        //抓放大底盘
        motor_run(getbig_deg1[0],getbig_deg2[0],getbig_deg3[0]);//抓大底盘
        delay(500);
        motor_run(getbig_deg1[1],getbig_deg2[1],getbig_deg3[1]);//抓大底盘
        delay(500);
        myservo.write(40);
        delay(500);
        motor_run(put_deg1[0],put_deg2[0],put_deg3[0]);//放大底盘
        delay(500);
        motor_run(put_deg1[1],put_deg2[1],put_deg3[1]);//放大底盘
        delay(500);
        myservo.write(0);
        delay(500);

        motor_return_to_zero();
      }
        roboflag++;
        break;

    default:
      break;
    }

    

  }
}

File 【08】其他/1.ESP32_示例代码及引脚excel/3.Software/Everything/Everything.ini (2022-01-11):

; Please make sure Everything is not running before modifying this file.
[Everything]
run_as_admin=1
window_x=145
window_y=160
window_wide=2337
window_high=1294
maximized=0
minimized=0
fullscreen=0
ontop=0
alpha=255
match_whole_word=0
match_path=0
match_case=0
match_diacritics=0
match_regex=0
view=0
thumbnail_size=64
thumbnail_fill=0
min_thumbnail_size=32
max_thumbnail_size=256
medium_thumbnail_size=64
large_thumbnail_size=128
extra_large_thumbnail_size=256
thumbnail_load_size=0
allow_multiple_windows=0
allow_multiple_instances=0
run_in_background=1
show_in_taskbar=1
show_tray_icon=1
minimize_to_tray=0
toggle_window_from_tray_icon=0
alternate_row_color=0
show_mouseover=0
check_for_updates_on_startup=0
beta_updates=0
show_highlighted_search_terms=1
text_size=0
hide_empty_search_results=0
clear_selection_on_search=1
show_focus_on_search=0
new_window_key=0
show_window_key=0
toggle_window_key=0
language=0
show_selected_item_in_statusbar=1
statusbar_selected_item_format=
show_size_in_statusbar=0
statusbar_size_format=0
open_folder_command2=
open_file_command2=
open_path_command2=
explore_command2=
explore_path_command2=
window_title_format=
taskbar_notification_title_format=
instance_name=
translucent_selection_rectangle_alpha=70
min_zoom=-6
max_zoom=27
context_menu_type=0
auto_include_fixed_volumes=1
auto_include_removable_volumes=0
auto_remove_offline_ntfs_volumes=1
auto_remove_moved_ntfs_volumes=1
auto_include_fixed_refs_volumes=1
auto_include_removable_refs_volumes=0
auto_remove_offline_refs_volumes=1
auto_remove_moved_refs_volumes=1
find_mount_points_on_removable_volumes=0
last_export_type=0
max_threads=0
reuse_threads=1
single_parent_context_menu=0
auto_size_1=512
auto_size_2=640
auto_size_3=768
auto_size_aspect_ratio_x=9
auto_size_aspect_ratio_y=7
auto_size_width_only=0
auto_size_path_x=1
auto_size_path_y=2
sticky_vscroll_bottom=1
last_options_page=0
draw_focus_rect=1
date_format=
time_format=
listview_item_high=0
single_click_open=0
underline_icon_titles=0
icons_only=0
auto_scroll_repeat_delay=250
auto_scroll_repeat_rate=50
open_many_files_warning_threshold=16
debug=0
debug_log=0
verbose=0
lvm=1
ipc=1
home_match_case=0
home_match_whole_word=0
home_match_path=0
home_match_diacritics=0
home_regex=0
home_search=1
home_filter=0
home_sort=0
home_view=0
home_index=1
allow_multiple_windows_from_tray=0
single_click_tray=0
close_on_execute=0
double_click_path=0
update_display_after_scroll=0
update_display_after_mask=1
auto_scroll_view=0
double_quote_copy_as_path=0
snap=0
snaplen=10
rename_select_filepart_only=0
rename_move_caret_to_selection_end=0
rename_nav=0
search_edit_move_caret_to_selection_end=0
select_search_on_mouse_click=1
focus_search_on_activate=0
reset_vscroll_on_search=1
wrap_focus=0
load_icon_priority=0
load_thumbnail_priority=0
load_fileinfo_priority=0
header_high=0
hide_on_close=0
winmm=0
menu_escape_amp=1
menu_folders=0
menu_folder_separator=
menu_items_per_column=0
new_inherit=1
full_row_select=0
tray_show_command_line=
dpi=96
ctrl_mouse_wheel_action=1
allow_open=1
allow_context_menu=1
allow_delete=1
allow_rename=1
allow_cut=1
allow_copy=1
allow_paste=1
allow_drag_drop=1
auto_column_widths=0
fast_ascii_search=1
match_path_when_search_contains_path_separator=1
allow_literal_operators=0
allow_round_bracket_parenthesis=0
expand_environment_variables=0
search_as_you_type=1
always_update_query_on_search_parameter_change=0
convert_forward_slash_to_backslash=0
match_whole_filename_when_using_wildcards=1
operator_precedence=0
replace_exact_trailing_star_dot_star_with_star=1
allow_exclamation_point_not=1
search_command_prefix=
double_buffer=1
search=
show_number_of_results_with_selection=0
date_descending_first=0
size_descending_first=0
size_format=2
alpha_select=0
tooltips=1
listview_tooltips=1
show_detailed_listview_tooltips=1
rtl_listview_edit=0
force_path_ltr_order=1
force_path_left_align=1
date_time_order=0
date_time_align=1
size_align=3
invert_layout=0
update_layout_on_input_language_change=0
control_shift_action=3
change_search_rtl_reading_action=3
invert_layout_action=3
bookmark_remember_case=1
bookmark_remember_wholeword=1
bookmark_remember_path=1
bookmark_remember_diacritic=1
bookmark_remember_regex=1
bookmark_remember_sort=1
bookmark_remember_view=1
bookmark_remember_filter=1
bookmark_remember_index=1
bookmark_remember_search=1
bookmark_organize_x=0
bookmark_organize_y=0
bookmark_organize_wide=0
bookmark_organize_high=0
exclude_list_enabled=1
exclude_hidden_files_and_folders=0
exclude_system_files_and_folders=0
include_only_files=
exclude_files=
db_location=
db_multi_user_filename=0
db_compress=0
index_size=1
fast_size_sort=1
index_date_created=0
fast_date_created_sort=0
index_date_modified=1
fast_date_modified_sort=1
index_date_accessed=0
fast_date_accessed_sort=0
index_attributes=0
fast_attributes_sort=0
index_folder_size=0
fast_path_sort=1
fast_extension_sort=0
extended_information_cache_monitor=1
db_update_thread_priority=-15
index_recent_changes=1
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

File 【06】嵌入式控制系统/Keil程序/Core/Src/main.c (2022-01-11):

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
/* Includes ------------------------------------------------------------------*/
#include "main.h"
#include "i2c.h"
#include "tim.h"
#include "usart.h"
#include "gpio.h"

/* USER CODE BEGIN Includes */
#include "oled.h"
#include "motor.h"
#include "linetracking.h"
#include "HC_SR04.h"
#include "delay.h"
#include "stdio.h"
#include "scheme.h"
/* USER CODE END Includes */

/* USER CODE BEGIN PTD */
extern HCSR04 hcsr04;
extern Situ_InitTypeDef vechile1;
/* USER CODE END PTD */

/* USER CODE BEGIN PD */
//#define INF1 HAL_GPIO_ReadPin(INF_port,INF_PIN_1)//右1
//#define INF2 HAL_GPIO_ReadPin(INF_port,INF_PIN_2)//右2
//#define INF3 HAL_GPIO_ReadPin(INF_port,INF_PIN_3)//左2
//#define INF4 HAL_GPIO_ReadPin(INF_port,INF_PIN_4)//左1
#define send_singal HAL_GPIO_WritePin(GoGo_GPIO_Port,GoGo_Pin,GPIO_PIN_SET)
#define close_singal HAL_GPIO_WritePin(GoGo_GPIO_Port,GoGo_Pin,GPIO_PIN_RESET)
#define START HAL_GPIO_ReadPin(Start_GPIO_Port,Start_Pin)
/* USER CODE END PD */


/* USER CODE BEGIN PV */
uint8_t flag_reach=0;
/* USER CODE END PV */

void SystemClock_Config(void);
/* USER CODE BEGIN PFP */
void getdistance(){
			if(hcsr04.STATE == TRIG_WAIT)
		{
			//给HCSR04一个50us触发电平
			HAL_GPIO_WritePin(TRIG_GPIO_Port,TRIG_Pin,GPIO_PIN_SET);
			Delay_us(20);			
			HAL_GPIO_WritePin(TRIG_GPIO_Port,TRIG_Pin,GPIO_PIN_RESET);
			
			//启动上升沿捕获
			__HAL_TIM_SET_CAPTUREPOLARITY(&HCSR04_TIM_HAL, HCSR04_TIM_CHANNEL, TIM_INPUTCHANNELPOLARITY_RISING);
			//启动输入捕获
			HAL_TIM_IC_Start_IT(&HCSR04_TIM_HAL, HCSR04_TIM_CHANNEL);	
			//设置上升沿捕获
			hcsr04.STATE = RISING;
		}
		
		if(hcsr04.STATE == OVER)//判断电平捕获结束
		{
			//计算高电平时间差值代表时间维持的长度，因为定时器设置1us自加一次，所以时长单位为us
			//乘以0.017的是因为声波速度为340m/s，而1s=1000000us，且记录一次距离是一个来回
			//要除以2，此处单位为cm
			hcsr04.len = (float)(hcsr04.buf[1]- hcsr04.buf[0])*0.017; 
			//刷新状态，使可以进行下一次触发电平
			hcsr04.STATE = TRIG_WAIT;
			//发送数据到上位机
			HAL_Delay(60);
	

		}
}
/* USER CODE END PFP */

/* USER CODE BEGIN 0 */
//char ch;
/* USER CODE END 0 */

/**
  * @brief  The application entry point.
  * @retval int
  */
int main(void)
{
  /* MCU Configuration--------------------------------------------------------*/

  /* Reset of all peripherals, Initializes the Flash interface and the Systick. */
  HAL_Init();

  /* Configure the system clock */
  SystemClock_Config();

  /* Initialize all configured peripherals */
  MX_GPIO_Init();
  MX_TIM3_Init();
  MX_TIM4_Init();
  MX_I2C1_Init();
  MX_TIM2_Init();
  MX_USART2_UART_Init();
  /* USER CODE BEGIN 2 */
	HAL_TIM_PWM_Start(&htim4,TIM_CHANNEL_2);  
	HAL_TIM_PWM_Start(&htim3,TIM_CHANNEL_3);
	
	OLED_Init();
	OLED_CLS();
	//STOP(0,100);
	uint8_t str1[10]="";
//	uint8_t str2[10]="";
//	uint8_t str3[10]="";
//	uint8_t str4[10]="";
//	uint8_t strdis[10]="";
	initilize_suit();
	//while(!START)

//	uint8_t a=0;
	
	
  /* USER CODE END 2 */

  /* Infinite loop */
  /* USER CODE BEGIN WHILE */
  while (1)
  {
    /* USER CODE END WHILE */

    /* USER CODE BEGIN 3 */
		
		sprintf ((char *)str1 ,"point:%d",vechile1.Trend);
//		sprintf ((char *)str2 ,"IO2:%d",INF2);
//		sprintf ((char *)str3 ,"IO3:%d",INF3);
//		sprintf ((char *)str4 ,"IO4:%d",INF4);
		OLED_ShowStr(0, 0, str1, 2);//显示字符串
//		OLED_ShowStr(0, 2, str2, 2);//显示字符串
//		OLED_ShowStr(0, 4, str3, 2);//显示字符串
//		OLED_ShowStr(0, 6, str4, 2);//显示字符串

		//getdistance();
		
//		if(hcsr04.len < 20.0)
//			STOP(0,20);	
//	else	
//	{
	//	 /*
		switch (vechile1.Trend)
		{
			case 0:
				while(!START)
				{
					STOP(0,500);
				}
				vechile1.Trend=1;
				break;
					
					
			case 1:
				line_follow();
				if(right90_check())
					{
						//STOP(0,2000);
						FORWARD(500,550);
						right_90(450,450,500);
						right_90turn();
						vechile1.Trend=2;
						//close_singal;
					}						
					break;
			case 2:
				line_follow();
				if( T_check() )
				{
					FORWARD(500,500);
					right_90(450,450,500);
					right_90turn();
					vechile1.Trend=3;		
				}
				break;
			case 3:
//				if( vechile1.turn_situ == 0  )
					circle_turn();
//				else if( vechile1.turn_situ ==1  )
//					line_follow();
				if( (right90_check() || T_check() ) && (vechile1.turn_situ==0) )
				{
					LEFTTURN(350,675,200);//左小转	 
					vechile1.turn_situ = 1;
				}
				
				else if( (right90_check() || T_check() ) && (vechile1.turn_situ==1) )
				{
					RIGHTTURN(520,450,650);
					right_90(450,450,650);
					right_90turn();	 
					vechile1.turn_situ = 0;
					vechile1.Trend=4;		
					//line_follow();
				}
				break;
				
			case 4:   //进到第一个路口抓物块
				line_follow();
				if( left90_check() )
					{
					FORWARD(500,530);
					left_90(450,450,300);
					left_90turn();
					vechile1.Trend=16;
					}
					break;
					
			case 16:
				line_follow_slowdown();
				if( T_check() )
				{
					FORWARD(300,250);
					STOP(0,500);
					send_singal;
					STOP(0,1000);
					close_singal;
					STOP(0,34000);
					vechile1.Trend=5;
				}
				break;
//			case 4:
//				line_follow();
//				if( T_check() )
//				{
//					STOP(0,2000);
//					vechile1.Trend=5;
//									
//				}
//				break;	
			case 5:
				BACK(350,2700);
				left_90(450,450,650);
				left_90turn();
				vechile1.Trend=7;	
				break;
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

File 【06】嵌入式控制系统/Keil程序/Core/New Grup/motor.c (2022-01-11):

#include "motor.h"
#include "tim.h"
//左转函数
/*  注：电机输入IO口1表示正转，0表示反转
				PWM口输入0--1000值进行速度调节
*/

void LEFTTURN(int C_COUNTER_L,int C_COUNTER_R,int TIME_L)
{     //左电机
	 //HAL_TIM_PWM_Start(&htim4,TIM_CHANNEL_2);                                    //开启左电机的pwm调压
	 __HAL_TIM_SET_COMPARE(&htim4, TIM_CHANNEL_2, C_COUNTER_L);                    //设定左电机的占空比=C_COUNTER/1000
	 HAL_GPIO_WritePin(LEFT_MOTOR_GPIO , LEFT_MOTOR_PIN, GPIO_PIN_RESET); //左轮正转      /* 设定IO的值使左转电机正转或反转  */  

		//右电机
	//	HAL_TIM_PWM_Start(&htim3,TIM_CHANNEL_3);                                   //开启右电机的pwm调压 
	 __HAL_TIM_SET_COMPARE(&htim3, TIM_CHANNEL_3, C_COUNTER_R*1.2);                     //设定右电机的占空比=C_COUNTER/1000
	 HAL_GPIO_WritePin(RIGHT_MOTOR_GPIO, RIGHT_MOTOR_PIN, GPIO_PIN_RESET);        /* 设定IO的值使右转电机正转或反转  */ 
	//设定运行时间
	   HAL_Delay(TIME_L);
	
//	   HAL_TIM_PWM_Stop(&htim4,TIM_CHANNEL_2);    //关闭左电机的pwm输出，防止怠速运行
//	   HAL_TIM_PWM_Stop(&htim3,TIM_CHANNEL_3);    //关闭右电机的pwm输出，防止怠速运行
}



//右转函数

void RIGHTTURN(int C_COUNTER_L,int C_COUNTER_R,int TIME_R)
{     //左电机
    // HAL_TIM_PWM_Start(&htim4,TIM_CHANNEL_2);                                    //开启左电机的pwm调压
		 __HAL_TIM_SET_COMPARE(&htim4, TIM_CHANNEL_2, C_COUNTER_L);                    //设定左电机的占空比=C_COUNTER/1000
     HAL_GPIO_WritePin(LEFT_MOTOR_GPIO , LEFT_MOTOR_PIN, GPIO_PIN_RESET);       /* 设定IO的值使左转电机正转或反转  */  
	
	    //右电机
	  //  HAL_TIM_PWM_Start(&htim3,TIM_CHANNEL_3);                                   //开启右电机的pwm调压 
		 __HAL_TIM_SET_COMPARE(&htim3, TIM_CHANNEL_3, C_COUNTER_R*1.12);                     //设定右电机的占空比=C_COUNTER/1000
     HAL_GPIO_WritePin(RIGHT_MOTOR_GPIO, RIGHT_MOTOR_PIN, GPIO_PIN_RESET);        /* 设定IO的值使右转电机正转或反转  */ 
	//设定运行时间
	   HAL_Delay(TIME_R);
	
//	   HAL_TIM_PWM_Stop(&htim4,TIM_CHANNEL_2);    //关闭左电机的pwm输出，防止怠速运行
//	   HAL_TIM_PWM_Stop(&htim3,TIM_CHANNEL_3);    //关闭右电机的pwm输出，防止怠速运行

}



//前进函数

void FORWARD(int C_COUNTER,int TIME)
{     //左电机
     //HAL_TIM_PWM_Start(&htim4,TIM_CHANNEL_2);                                    //开启左电机的pwm调压
		 __HAL_TIM_SET_COMPARE(&htim4, TIM_CHANNEL_2, C_COUNTER);                    //设定左电机的占空比=C_COUNTER/1000
     HAL_GPIO_WritePin(LEFT_MOTOR_GPIO , LEFT_MOTOR_PIN, GPIO_PIN_RESET);       /* 设定IO的值使左转电机正转或反转  */  
	
	    //右电机
	 //  HAL_TIM_PWM_Start(&htim3,TIM_CHANNEL_3);                                   //开启右电机的pwm调压 
		 __HAL_TIM_SET_COMPARE(&htim3, TIM_CHANNEL_3, C_COUNTER*1.12);                     //设定右电机的占空比=C_COUNTER/1000
     HAL_GPIO_WritePin(RIGHT_MOTOR_GPIO, RIGHT_MOTOR_PIN, GPIO_PIN_RESET);        /* 设定IO的值使右转电机正转或反转  */ 
	//设定运行时间
	   HAL_Delay(TIME);
	
	  // HAL_TIM_PWM_Stop(&htim4,TIM_CHANNEL_2);    
	  // HAL_TIM_PWM_Stop(&htim3,TIM_CHANNEL_3);    //关闭左右电机的pwm输出，防止怠速运行
}


//后退函数


void BACK(int C_COUNTER,int TIME)
{     //左电机
     //HAL_TIM_PWM_Start(&htim4,TIM_CHANNEL_2);                                    //开启左电机的pwm调压
		 __HAL_TIM_SET_COMPARE(&htim4, TIM_CHANNEL_2, C_COUNTER);                    //设定左电机的占空比=C_COUNTER/1000
     HAL_GPIO_WritePin(LEFT_MOTOR_GPIO , LEFT_MOTOR_PIN, GPIO_PIN_SET);       /* 设定IO的值使左转电机正转或反转  */  
	
	    //右电机
	 //  HAL_TIM_PWM_Start(&htim3,TIM_CHANNEL_3);                                   //开启右电机的pwm调压 
		 __HAL_TIM_SET_COMPARE(&htim3, TIM_CHANNEL_3, C_COUNTER*1.12);                     //设定右电机的占空比=C_COUNTER/1000
     HAL_GPIO_WritePin(RIGHT_MOTOR_GPIO, RIGHT_MOTOR_PIN, GPIO_PIN_SET);        /* 设定IO的值使右转电机正转或反转  */ 
	//设定运行时间
	   HAL_Delay(TIME);
	
	  // HAL_TIM_PWM_Stop(&htim4,TIM_CHANNEL_2);    
	  // HAL_TIM_PWM_Stop(&htim3,TIM_CHANNEL_3);    //关闭左右电机的pwm输出，防止怠速运行
}



//制动函数

void STOP(int C_COUNTER,int TIME)
{     //左电机
	//HAL_TIM_PWM_Start(&htim4,TIM_CHANNEL_2);     //开启左电机的pwm调压	  
	//HAL_TIM_PWM_Start(&htim3,TIM_CHANNEL_3);     //开启右电机的pwm调压     
                          
	__HAL_TIM_SET_COMPARE(&htim4, TIM_CHANNEL_2, C_COUNTER);   //设定左电机的占空比=C_COUNTER/1000	
	__HAL_TIM_SET_COMPARE(&htim3, TIM_CHANNEL_3, C_COUNTER);   //设定右电机的占空比=C_COUNTER/1000
	 HAL_Delay(TIME);
	// HAL_TIM_PWM_Stop(&htim4,TIM_CHANNEL_2);    //关闭左电机的pwm输出，防止怠速运行
	 //HAL_TIM_PWM_Stop(&htim3,TIM_CHANNEL_3);    //关闭右电机的pwm输出，防止怠速运行
}
void left_90(int C_COUNTER_L,int C_COUNTER_R,int TIME)
{     //左电机
	//HAL_TIM_PWM_Start(&htim4,TIM_CHANNEL_2);     //开启左电机的pwm调压	  
	//HAL_TIM_PWM_Start(&htim3,TIM_CHANNEL_3);     //开启右电机的pwm调压     
  HAL_GPIO_WritePin(LEFT_MOTOR_GPIO , LEFT_MOTOR_PIN, GPIO_PIN_SET); //左轮反转      /* 设定IO的值使左转电机正转  */  
	HAL_GPIO_WritePin(RIGHT_MOTOR_GPIO, RIGHT_MOTOR_PIN, GPIO_PIN_RESET);        /* 设定IO的值使右转电机正转  */ 
	
	__HAL_TIM_SET_COMPARE(&htim4, TIM_CHANNEL_2, C_COUNTER_L);   //设定左电机的占空比=C_COUNTER/1000	
	__HAL_TIM_SET_COMPARE(&htim3, TIM_CHANNEL_3, C_COUNTER_R*1.12);   //设定右电机的占空比=C_COUNTER/1000

	HAL_Delay(TIME);
	// HAL_TIM_PWM_Stop(&htim4,TIM_CHANNEL_2);    //关闭左电机的pwm输出，防止怠速运行
	 //HAL_TIM_PWM_Stop(&htim3,TIM_CHANNEL_3);    //关闭右电机的pwm输出，防止怠速运行
}
void right_90(int C_COUNTER_L,int C_COUNTER_R,int TIME)
{     //左电机
	//HAL_TIM_PWM_Start(&htim4,TIM_CHANNEL_2);     //开启左电机的pwm调压	  
	//HAL_TIM_PWM_Start(&htim3,TIM_CHANNEL_3);     //开启右电机的pwm调压     
  HAL_GPIO_WritePin(LEFT_MOTOR_GPIO , LEFT_MOTOR_PIN, GPIO_PIN_RESET); //左轮反转      /* 设定IO的值使左转电机正转  */  
	HAL_GPIO_WritePin(RIGHT_MOTOR_GPIO, RIGHT_MOTOR_PIN, GPIO_PIN_SET);        /* 设定IO的值使右转电机正转  */ 
                        
	__HAL_TIM_SET_COMPARE(&htim4, TIM_CHANNEL_2, C_COUNTER_L);   //设定左电机的占空比=C_COUNTER/1000	
	__HAL_TIM_SET_COMPARE(&htim3, TIM_CHANNEL_3, C_COUNTER_R);   //设定右电机的占空比=C_COUNTER/1000

	HAL_Delay(TIME);
	// HAL_TIM_PWM_Stop(&htim4,TIM_CHANNEL_2);    //关闭左电机的pwm输出，防止怠速运行
	 //HAL_TIM_PWM_Stop(&htim3,TIM_CHANNEL_3);    //关闭右电机的pwm输出，防止怠速运行
}

void rotate_180(int C_COUNTER_L,int C_COUNTER_R,int TIME)
{     //左电机
	//HAL_TIM_PWM_Start(&htim4,TIM_CHANNEL_2);     //开启左电机的pwm调压	  
	//HAL_TIM_PWM_Start(&htim3,TIM_CHANNEL_3);     //开启右电机的pwm调压     
  HAL_GPIO_WritePin(LEFT_MOTOR_GPIO , LEFT_MOTOR_PIN, GPIO_PIN_RESET); //左轮反转      /* 设定IO的值使左转电机正转  */  
	HAL_GPIO_WritePin(RIGHT_MOTOR_GPIO, RIGHT_MOTOR_PIN, GPIO_PIN_SET);        /* 设定IO的值使右转电机正转  */                         
	__HAL_TIM_SET_COMPARE(&htim4, TIM_CHANNEL_2, C_COUNTER_L);   //设定左电机的占空比=C_COUNTER/1000	
	__HAL_TIM_SET_COMPARE(&htim3, TIM_CHANNEL_3, C_COUNTER_R);   //设定右电机的占空比=C_COUNTER/1000

	HAL_Delay(TIME);
	// HAL_TIM_PWM_Stop(&htim4,TIM_CHANNEL_2);    //关闭左电机的pwm输出，防止怠速运行
	 //HAL_TIM_PWM_Stop(&htim3,TIM_CHANNEL_3);    //关闭右电机的pwm输出，防止怠速运行
}

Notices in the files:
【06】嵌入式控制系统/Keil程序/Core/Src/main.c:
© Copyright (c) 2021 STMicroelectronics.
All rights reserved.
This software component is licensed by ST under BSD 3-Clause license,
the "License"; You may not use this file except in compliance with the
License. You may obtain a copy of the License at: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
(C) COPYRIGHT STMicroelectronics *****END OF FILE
